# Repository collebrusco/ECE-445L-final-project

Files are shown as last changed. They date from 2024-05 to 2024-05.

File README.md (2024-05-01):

# ECE445L Final Lab
Final project for Spring '24 ECE 445L (1st place winner!)    
Frank Collebrusco, Rocco Perciavalle, Connor Leu, Sajid Bhuiyan      

Remote-controlled drag racing! Players use two controllers to drive the dragsters. The controllers have a throttle and a gear shifter, and the players must time their gear shifts for the optimal power output. The controller software simulates engine operation and the resulting power output. Players are penalized for red-lining, shifting too early or too late. The better driver wins!   

team photo

dragsters   

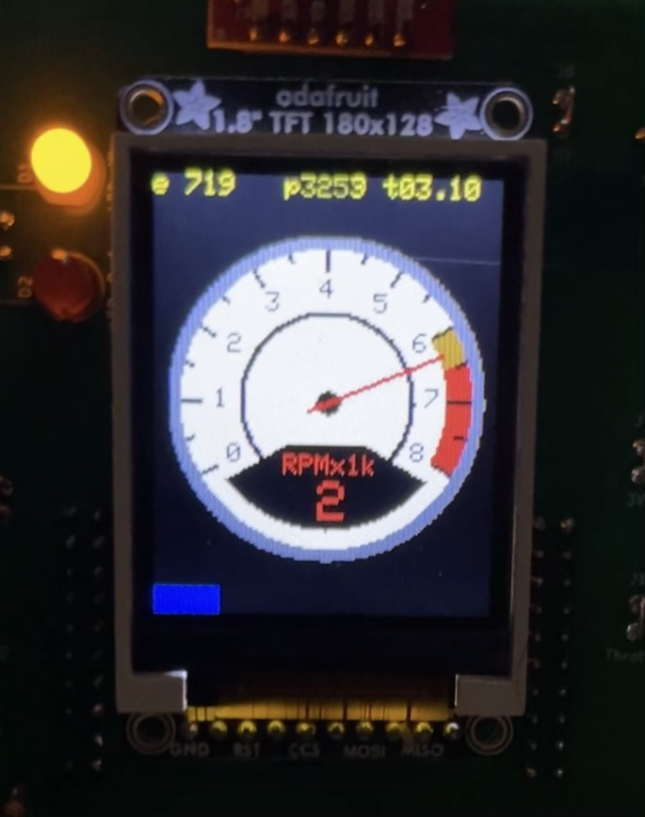
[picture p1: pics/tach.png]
tach


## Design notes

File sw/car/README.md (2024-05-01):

# README

This is the template project folder for your lab. Feel free to modify the files
in here, as long as they remain in this folder. This is where TAs will look for
when running your project and/or inspecting your code for software quality.

## Creating a New Project (Keil)

1. Open up Keil.
2. Click on the 'Project' tab on the top toolbar.
3. Click on New uVision Project.
4. Create a new .uvproj file of the desired name (typically Lab1, Lab5, etc) in the SW folder.
5. Search for the 'TM4C123GH6PM' device in the 'Select Device for Target 'Target 1' window.
6. Press OK and then press OK again in the 'Manage Run-Time Environment' window. 

## Managing Project Files

1. Right click on the 'Target 1' item in the Project sidebar window.
2. Click on 'Manage Project Items' in the submenu.
3. In the 'Files' column, click on the 'Add Files' button.
4. Add the implementation files (.C and .s files) required for the project
   dependencies into the project. This includes your main file. In particular,
   make sure you include the startup.s file, since this includes things like
   interrupt definitions.

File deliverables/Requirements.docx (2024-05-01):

## Project Requirements Document:

1) Overview
  a) Objectives: Why are we doing this project? What is the purpose?

The goal of this project is to combine what we’ve learned through the labs in this class as well as prior 319K knowledge into a coherent embedded system. The project provides a more open-ended scenario than the other labs which allows us to build a more creative system and see the creativity of other groups.

  b) Interactions with Existing Systems: Include this if you are connecting to another board

Aside from using multiple TM4Cs, we will be interfacing via UART with ESP8266 microcontrollers for wireless communication. The goal is to minimize complexity of the networking protocol and have two ESP microcontrollers communicating with each other directly.

  c) Terminology: Define domain specific terms used in the document.

None.

2) Functional Description
  a) Functionality: What will the system do precisely?

The system is a slot-car racing game. The game is two players, each with a car on a racetrack. Skill from the game is derived from controlling your speed around turns (you need to avoid flying off the track!) and timing your “shifting” to maximize your speed. The system will have two controllers that wirelessly communicate with their car, and a central TM4C for timing and/or counting laps, declaring the winner, and potentially additional stretch-goals.

  b) Performance: Define the measures and describe how they will be determined.

Performance of this system will be measured through controller latency, timing latency, and speed and maneuverability of the cars. Controller latency could be measured via synchronous clocks on each system, and seeing the time elapsed between an input and seeing movement on the car, or through a slow-motion video. Speed an maneuverability of the cars can be measured by simply observing them move around the track.

  c) Usability: Describe the interfaces. Be quantitative if possible

The main interfaces for the users in the system are the controllers. There will be two sets of controls, one for each car. The controller will not be battery operated. Instead, it will be wired to the track. The controllers will then communicate wirelessly to the cars. As a stretch goal, we intend to have speedometers and other metrics on LCDs as part of the controller.

3) Deliverables
  a) Roles and Responsibilities: Who will do what? What is the purpose?

Conner Leu will be largely responsible for designing the PCBs, and sourcing components. Frank Collebrusco and Sajid Bhuiyan will work heavily on the software managing wireless, timing, and potentially graphical systems. Rocco Perciavalle will work on 3D CAD models for the car chassis. All members will provide support across all aspects of the project, including building the track, cars, controllers, and software.

  b) Reports: Simply state the reports for Labs 7 and 11 will be written

Reports for Labs 7 and 11 will be written.

  c) Outcomes: What are the deliverables? How do we know when it is done?

The project is done once we have two functional cars and controllers that communicate wirelessly, along with a central controller to manage laps and timing. Any additional features are stretch goals.

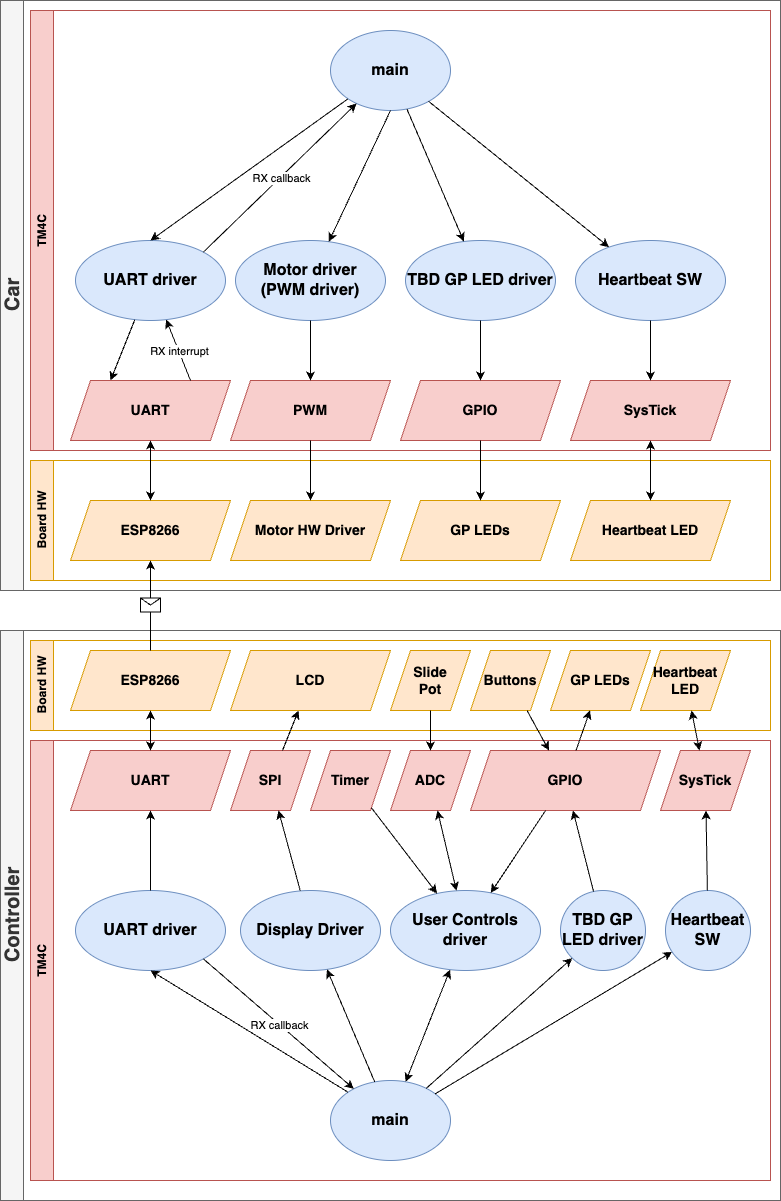
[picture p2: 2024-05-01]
deliverables/SystemDiagram.png

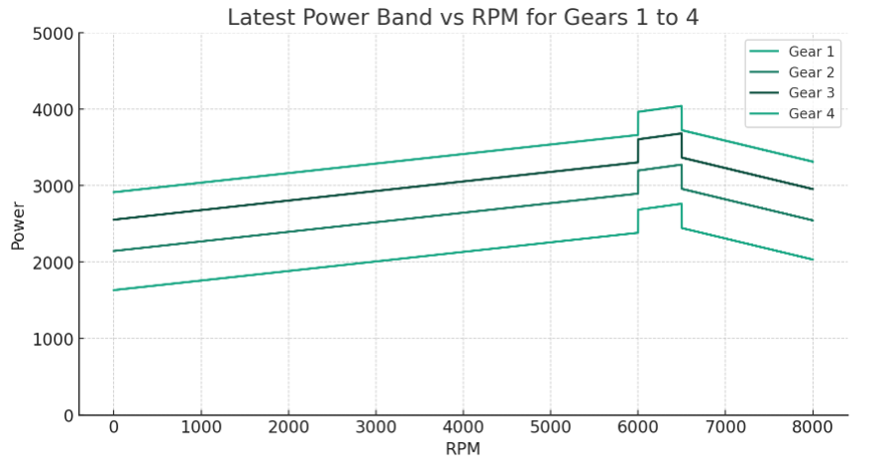
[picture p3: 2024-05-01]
sw/PWM_12bit_by_rpm_gear.PNG

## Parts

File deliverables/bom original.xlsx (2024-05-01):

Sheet: Parts
Bill of Materials |  |  | 2022-03-10 | "not free" means you have to buy it |  | "free sample" means you have to order it
EE445L Spring 2022 |  |  | EE445L pays for the PCB | "Cabinet means in one of the six black cabinets in professsor's office (bring a print out of your SCH")
 |  |  |  | "Professor" means ask your professor quantity and style will vary (bring a print out of your SCH circuit)
Qty Note | REF DES Note (http://projects.ece.utexas.edu/valvano/wiki/doku.php?id=pcbartist:schematics) |  |  | "Box means in box in your professor's office (bring a print out of your SCH circuit)
Quantity | REF DES | Type | Description | Manufacturer | Mfg. P/N | Distributor | P/N | Unit cost | Cost |  | Where to get it? | Inventory
0 |  | ASM | 8-ohm speaker |  |  | AllElectronics | SK-840 | $0.60 | $0.00 | Speaker | professor | https://www.allelectronics.com/item/sk-840/speaker-8-ohm-40mm/1.html
0 |  | ASM | 9V battery snap, T-type |  |  | AllElectronics | BST-61 | $0.50 | $0.00 | Jumper2 | Box
0 |  | ASM | Black case, 5.5" x 2.6" x 1.1" | Hammond | 1593YALBK | Mouser | 546-1593YALBK | $8.50 | $0.00 |  |  | http://www.hammondmfg.com/pdf/1593Y.pdf
0 |  | ASM | Black Case 5.620" x 3.250" X 1.500" | Serpac | 151 | Digikey | SR151B-ND | $10.88 | $0.00 |  | professor
0 |  | ASM | Black case, 7.5" by 4.3" by 2.2" | Hammond | 1591ESBK | Mouser | 546-1591ES-BK | $8.71 | $0.00 |  | Box | http://www.hammondmfg.com/pdf/1591E.pdf
0 |  | ASM | Electret microphone | Panasonic |  | AllElectronics | MIKE-79 | $0.50 | $0.00 | electret | Cabinet
0 |  | CAP | Ceramic, X7R, 20%, 1 uF |  |  | Jameco | 81509 | $0.35 | $0.00 | Ceramic0.2 | Cabinet
0 |  | CAP | Ceramic, Z5U, -20/+80%, 0.47 uF | Kemet | C320C474M5U5TA | Digikey | 399-4309-ND | $0.40 | $0.00 | Ceramic | Cabinet
0 |  | CAP | Ceramic, Z5U, -20/+80%, 0.1 uF |  |  | Digikey | 399-4151-ND | $0.04 | $0.00 | Ceramic | Cabinet
0 |  | CAP | Ceramic, Z5U, -20/+80%, 0.033 uF |  |  | Digikey | 399-4298-ND | $0.40 | $0.00 | Ceramic | Cabinet
0 |  | CAP | Ceramic, Z5U, -20/+80%, 0.027uF |  |  |  |  | $0.40 | $0.00 | Ceramic | Cabinet
0 |  | CAP | Ceramic, Z5U, -20/+80%, 0.01 uF |  |  | Digikey | 399-4148-ND | $0.40 | $0.00 | Ceramic | Cabinet
0 |  | CAP | Ceramic, Z5U, -20/+80%, 4.7 nF |  |  | Digikey | 399-4188-ND | $0.40 | $0.00 | Ceramic | Cabinet
0 |  | CAP | Ceramic, Z5U, -20/+80%, 2.2 nF |  |  |  |  | $0.40 | $0.00 | Ceramic | Cabinet
0 |  | CAP | Ceramic, Z5U, -20/+80%, 1 nF |  |  |  |  | $0.40 | $0.00 | Ceramic | Cabinet
0 |  | CAP | Ceramic Z5U, -20/+80%, 470 pF |  |  |  |  | $0.03 | $0.00 | Ceramic | Cabinet
0 |  | CAP | Ceramic Z5U, -20/+80%, 330 pF |  |  |  |  | $0.03 | $0.00 | Ceramic | Cabinet
0 |  | CAP | Ceramic Z5U, -20/+80%, 220 pF |  |  |  |  | $0.03 | $0.00 | Ceramic | Cabinet
0 |  | CAP | Ceramic Z5U, -20/+80%, 100 pF |  |  |  |  | $0.03 | $0.00 | Ceramic | Cabinet
0 |  | CAP | Ceramic Z5U, -20/+80%, 22 pF |  |  |  |  | $0.03 | $0.00 | Ceramic | Cabinet
0 |  | CAP | Ceramic C0G, 10%, 10 pF | Murata 50V 5% | RDE5C1H100J0P1H03B | Digikey | 490-8629-ND | $0.31 | $0.00 | Ceramic | Cabinet | not required, we expect most students will create a system with the LaunchPad
0 |  | CAP-Tant | Tantalum, 16V, 20% 2.2 uF | AVX Corporation | TAP225M016CCS | Digikey | 478-8819-ND | $0.29 | $0.00 | tantalum | Cabinet
0 |  | CAP-Tant | Tantalum, 16V, 10% 4.7 uF |  |  | Digikey | 478-1904-ND | $0.22 | $0.00 | tantalum | Cabinet
0 |  | CAP-Tant | Tantalum, 20V, 10%, 1 uF |  |  | Digikey | 478-1833-ND | $0.32 | $0.00 | tantalum | Cabinet
0 |  | CAP-Tant | Tantalum, 20V 10%, 10uF |  |  | Digikey | 478-1840-ND | $0.56 | $0.00 | tantalum | Cabinet
0 |  | CAP-Tant | Tantalum, 35V, 10%, 0.47 uF |  |  | Jameco | 33531 | $0.19 | $0.00 | tantalum | Cabinet
0 |  | CAP-Elec | Electrolytic, 16V, 100 uF, cap 20%, ESR=20mV |  |  | Mouser | 661-APSF160E101MF05S | $0.38 | $0.00 | tantalum | Cabinet
0 |  | CON | 2 to 40 pin 0.1 in header (price per pin) |  |  | AllElectronics | SHS-40 | $0.02 | $0.00 | Jumper2 | Cabinet | https://www.allelectronics.com/item/shs-40/1-x-40-header-0.1-spacing/1.html
0 |  | CON | 2-pin shrouded header (mates with SBC-2) |  |  | AllElectronics | SBH-2 | $0.10 | $0.00 | Jumper2 | Cabinet | https://www.allelectronics.com/item/sbh-2/header-for-small-battery-conn-2.5mm-spacing/1.html
0 |  | CON | 2-pin battery cable (mates with SBH-2) |  |  | AllElectronics | SBC-2 | $0.27 | $0.00 | goes with SBH-2 | Cabinet | https://www.allelectronics.com/item/sbc-2/small-battery-connector-2.5mm-spacing/1.html
0 |  | CON | 2-pin shorting jumper, attaches to 0.1" male-male header | Harwin | M7581-05 | Mouser | 855-M7581-05 | $0.11 | $0.00 | goes with Jumper2 | Cabinet
0 |  | CON | Test point, black | Keystone Electronics | 5001 | Digikey | 36-5001K-ND | $0.23 | $0.00 | testpoint | Cabinet
0 |  | CON | Test point, orange | Keystone Electronics | 5003 | Digikey | 36-5003K-ND | $0.23 | $0.00 | testpoint | Cabinet
0 |  | CON | Test point, yellow | Keystone Electronics | 5004 | Digikey | 36-5004K-ND | $0.23 | $0.00 | testpoint | Cabinet
0 |  | CON | Test point, white | Keystone Electronics | 5002 | Digikey | 36-5002K-ND | $0.23 | $0.00 | testpoint | Cabinet
0 |  | CON | Test point, blue | Keystone Electronics | 5117 | Digikey | 36-5117-ND | $0.23 | $0.00 | testpoint | Cabinet
0 |  | CON | Test point, green | Keystone Electronics | 5116 | Digikey | 36-5116-ND | $0.23 | $0.00 | testpoint | Cabinet
0 |  | CON | Test point, red | Keystone Electronics | 5000 | Digikey | 36-5000K-ND | $0.23 | $0.00 | testpoint | Cabinet
0 |  | CON | 10-pin female connector | SamTec | BCS-110-L-S-TE | Digikey | SAM1011-10-ND | $1.98 | $0.00 |  | Cabinet
0 |  | CON | Socket for micro SD card | Molex | 473340001 | Digikey | WM3288CT-ND | $4.02 | $0.00 | MicroSD Slot | Cabinet | do not use, rather included on ST7735
0 |  | CON | USB Mini-B socket, board mount, surface mount | Molex | 56579-0576 | Mouser | 538-56579-0576 | $2.46 | $0.00 | USB_Mini-B | Cabinet
0 |  | CON | Micro USB Type B, surface mount | Hirose Connector | ZX62D-B-5PA8(30) | Mouser | 798-ZX62D-B-5PA830 | $0.47 | $0.00 | USB_Micro-B | Cabinet
0 |  | CON | USB Mini-B socket, board mount, through hole | Molex | 54819-0519 | Digikey | WM17115-ND | $0.65 | $0.00 | USB_Mini-B | Cabinet
0 |  | CON | BoosterPack connector | FCI | 67996-220HLF | Mouser | 609-3243-ND | $0.26 | $0.00 | BoosterPack | Cabinet
0 |  | CON | Logic Analyzer connector | FCI | 68021-208HLF | Digikey | 609-3344-ND | $0.27 | $0.00 | LogicAnalyzer | Cabinet
0 |  | CON | JTAG 1 by 5 male header |  |  |  |  | $0.29 | $0.00 | JTAG | Cabinet
0 |  | CON | 10 pin 2mm socket for Xbee (need two) | SamTec | SQT-110-01-F-S | Digikey | SAM9989-ND | $2.70 | $0.00 | XbeeModule | Cabinet
0 |  | CPU | TM4C123GH6PM 64-pin LQFP | TI | TM4C123GH6PMI | Mouser | 595-TM4C123GH6PMI | $11.55 | $0.00 | TM4C123GH6PM |  | not required, we expect most students will create a system with the LaunchPad
0 |  | CRYS | NX5032GA-16.000000 | NDK | NX5032GA-16.000000 | Digikey | 644-1037-1-ND | $0.51 | $0.00 | XTAL/NX5032 | Cabinet | not required, we expect most students will create a system with the LaunchPad
0 |  | DIODE | 1N914 diode | Fairchild | 1N914 | Digikey | 1N914B-ND | $0.05 | $0.00 | 1N914 | Cabinet
0 |  | IC | LM2937 3.3 V regulator TO220, 500mA | TI | LM2937ET-3.3/NOPB | Digikey | LM2937ET-3.3-ND | $1.17 | $0.00 | LM2937-3.3 | Cabinet
0 |  | IC | LP2950 3.3V regulator, 100 mA TO-92 | TI | LP2950-33LPRE3 | Digikey | 296-31455-1-ND | $0.19 | $0.00 | LP2950-CZ-3.3 | Cabinet
0 |  | IC | 78M05 500mA 5V TO-220 regulator | National | LM78M05 | Jameco | 192233 | $0.19 | $0.00 | LM7805CT | Cabinet
0 |  | IC | OPA4350 quad op amp | TI | OPA4350UA | Mouser | 595-OPA4350UA | $12.15 | $0.00 | OPA4350 | not free
0 |  | IC | TLV5616 12-bit DAC | TI | TLV5616CP | Mouser | 595-TLV5616CP | $10.09 | $0.00 | TLV5616 | not free
0 |  | IC | TLV5618 dual 12-bit DAC | TI | TLV5618 | Mouser | TLV5618ACP | $14.18 | $0.00 | TLV5618 | not free
0 |  | IC | INA122P instrumentation amp | TI | INA122P | Mouser | 595-INA122P | $9.09 | $0.00 | INA122 | Cabinet or free sample
0 |  | IC | OPA2350 dual op amp | TI | OPA2350PA | obsolete |  |  | $0.00 | OPA2350 | Cabinet or free sample |  |  | 1 KD
0 |  | IC | TLC2274 quad op amp | TI | TLC2274ACN | Mouser | 595-TLC2274ACN | $3.06 | $0.00 | TLC2274 | not free |  |  | 2 HD
0 |  | IC | TPA731 audio amp (pin 1 low) 700mW | TI | TPA731D | Mouser | 595-TPA731D | $2.90 | $0.00 | TPA731 | not free |  |  | 3 AD
0 |  | IC | TPA751 audio amp (pin 1 high) 700mW | TI | TPA751D | Mouser | 595-TPA751D | $2.31 | $0.00 | TPA731 | not free |  |  | 4 JD
0 |  | IC | LM4041CILPR shunt diode reference | TI | LM4041CILPR | Mouser | 595-LM4041CILPR | $1.21 | $0.00 | LM4041 | Cabinet or free sample |  |  | 5 CD
0 |  | IC | L293 Motor H bridge | TI | L293NE | Digikey | 296-9519-5-ND | $3.50 | $0.00 | L293 | Cabinet |  |  | 7 MD
0 |  | IC | 74HC595 |  |  | Jameco | 46105 | $0.40 | $0.00 |  | Cabinet |  |  | 8 ED
0 |  | IC | 74HC165 |  |  | Jameco | 45495 | $0.30 | $0.00 |  | Cabinet |  |  | 9 FD
0 |  | IC | 74HCT125N | TI | SN74HCT125N | Mouser | 595-SN74HCT125N | $0.53 | $0.00 |  | Cabinet
0 |  | IC | RS232 driver | STMicroelectronics | ST232CN | Jameco | 2001171 | $0.58 | $0.00 | ST232 | Cabinet |  |  | 0 ND
0 |  | JACK | DC Power MALE 2.1mm |  |  | Jameco | 101179 | $0.55 | $0.00 | PowerJack | Cabinet |  |  | * LD
0 |  | JACK | Stereo Jack, or audio jack |  |  | AllElectronics | MJW-12 | $0.09 | $0.00 | HeadphoneJack | Cabinet |  | 87YY3212A
0 |  | KEY | 3 by 4 common bus (D), keypad | Grayhill | 87YY3212A-506 |  |  | $2.99 | $0.00 | 87YY3212A | Box | http://docs.bgmicro.com/pdf/swt1109.pdf
0 |  | LCD | 18-bit color 128*160 1.8" TFT LCD display | Sitronix | ST7735R | Adafruit | 358 | $19.96 | $0.00 | ST7735 | not free
0 |  | LED | Green 2mA 5mm diffused | Avago Technologies | HLMP-4740 | Digikey | 516-1327-ND | $0.29 | $0.00 | LEDT1.75 | Cabinet
0 |  | LED | Red 1.6V 1mA 5mm diffused | Avago Technologies | HLMP-D150 | Digikey | 516-1323-ND | $0.29 | $0.00 | LEDT1.75 | Cabinet
0 |  | LED | Yellow 2mA 5mm diffused | Avago Technologies | HLMP-4719 | Digikey | 516-1326-ND | $0.29 | $0.00 | LEDT1.75 | Cabinet
0 |  | LED | Orange 10mA 5mm diffused | Avago Technologies | HLMP-D401 | Digikey | 516-1330-ND | $0.29 | $0.00 | LEDT1.75 | Cabinet
0 |  | LED | Blue 10mA 5mm diffused |  |  |  |  | $0.99 | $0.00 | LEDT1.75 | Cabinet | warning, the blue LEDs are very bright
0 |  | PCB | PCB plus shipping | JLCPCB |  | JLCPCB |  | $13.00 | $0.00
0 |  | POT | 20K LINEAR SLIDE POT | Bourns | PTA2043-2015CPB103 | Mouser | 652-PTA20432015CPB10 | $1.28 | $0.00 |  | Cabinet
0 |  | POT | 10 K one-turn potentiometer |  |  |  |  | $0.15 | $0.00 | SquarePot | Professor
0 |  | POT | 20 K one-turn potentiometer |  |  |  |  | $0.15 | $0.00 | SquarePot | Professor
0 |  | RES | Carbon 1/6W, 5%, 100 | Yageo | CFR-12JB-100R | Digikey | 100EBK-ND | $0.02 | $0.00 | 0.125Wresistor | Cabinet
0 |  | RES | Carbon 1/6W, 5%, 220 | Yageo | CFR-12JB-220R | Digikey | 220EBK-ND | $0.02 | $0.00 | 0.125Wresistor | Cabinet
0 |  | RES | Carbon 1/6W, 5%, 270 | Yageo | CFR-12JB-270R | Digikey | 270EBK-ND | $0.02 | $0.00 | 0.125Wresistor | Cabinet
0 |  | RES | Carbon 1/6W, 5%, 330 | Yageo | CFR-12JB-330R | Digikey | 330EBK-ND | $0.02 | $0.00 | 0.125Wresistor | Cabinet
0 |  | RES | Carbon 1/6W, 5%, 470 | Yageo | CFR-12JB-470R | Digikey | 470EBK-ND | $0.02 | $0.00 | 0.125Wresistor | Cabinet
0 |  | RES | Carbon 1/6W, 5%, 510 | Yageo | CFR-12JB-510R | Digikey | 510EBK-ND | $0.02 | $0.00 | 0.125Wresistor | Cabinet
0 |  | RES | Carbon 1/6W, 5%, 680 | Yageo | CFR-12JB-680R | Digikey | 680EBK-ND | $0.02 | $0.00 | 0.125Wresistor | Cabinet
0 |  | RES | Carbon 1/6W, 5%, 820 | Yageo | CFR-12JB-820R | Digikey | 820EBK-ND | $0.02 | $0.00 | 0.125Wresistor | Cabinet
0 |  | RES | Carbon 1/6W, 5%, 1K | Yageo | CFR-12JB-1K0 | Digikey | 1.0KEBK-ND | $0.02 | $0.00 | 0.125Wresistor | Cabinet
0 |  | RES | Carbon 1/6W, 5%, 1.2K | Yageo | CFR-12JB-1K2 | Digikey | 1.2KEBK-ND | $0.02 | $0.00 | 0.125Wresistor | Cabinet
0 |  | RES | Carbon 1/6W, 5%, 1.5K | Yageo | CFR-12JB-1K5 | Digikey | 1.5KEBK-ND | $0.02 | $0.00 | 0.125Wresistor | Cabinet
0 |  | RES | Carbon 1/6W, 5%, 1.8K | Yageo | CFR-12JB-1K8 | Digikey | 1.8KEBK-ND | $0.02 | $0.00 | 0.125Wresistor | Cabinet
0 |  | RES | Carbon 1/6W, 5%, 2.0K | Yageo | CFR-12JB-2K0 | Digikey | 2.0KEBK-ND | $0.02 | $0.00 | 0.125Wresistor | Cabinet
0 |  | RES | Carbon 1/6W, 5%, 2.2K | Yageo | CFR-12JB-2K2 | Digikey | 2.2KEBK-ND | $0.02 | $0.00 | 0.125Wresistor | Cabinet
0 |  | RES | Carbon 1/6W, 5%, 2.7K | Yageo | CFR-12JB-2K7 | Digikey | 2.7KEBK-ND | $0.02 | $0.00 | 0.125Wresistor | Cabinet
0 |  | RES | Carbon 1/6W, 5%, 3.3K | Yageo | CFR-12JB-3K3 | Digikey | 3.3KEBK-ND | $0.02 | $0.00 | 0.125Wresistor | Cabinet
0 |  | RES | Carbon 1/6W, 5%, 3.9K | Yageo | CFR-12JB-3K9 | Digikey | 3.9KEBK-ND | $0.02 | $0.00 | 0.125Wresistor | Cabinet
0 |  | RES | Carbon 1/6W, 5%, 4.7K | Yageo | CFR-12JB-4K7 | Digikey | 4.7KEBK-ND | $0.02 | $0.00 | 0.125Wresistor | Cabinet
0 |  | RES | Carbon 1/6W, 5%, 5.1K | Yageo | CFR-12JB-5K1 | Digikey | 5.1KEBK-ND | $0.02 | $0.00 | 0.125Wresistor | Cabinet
0 |  | RES | Carbon 1/6W, 5%, 5.6K | Yageo | CFR-12JB-5K6 | Digikey | 5.6KEBK-ND | $0.02 | $0.00 | 0.125Wresistor | Cabinet
0 |  | RES | Carbon 1/6W, 5%, 6.8K | Yageo | CFR-12JB-6K8 | Digikey | 6.8KEBK-ND | $0.02 | $0.00 | 0.125Wresistor | Cabinet
0 |  | RES | Carbon 1/6W, 5%, 8.2K | Yageo | CFR-12JB-8K2 | Digikey | 8.2KEBK-ND | $0.02 | $0.00 | 0.125Wresistor | Cabinet
0 |  | RES | Carbon 1/6W, 5%, 10K | Yageo | CFR-12JB-10K | Digikey | 10KEBK-ND | $0.02 | $0.00 | 0.125Wresistor | Cabinet
0 |  | RES | Carbon 1/6W, 5%, 12K | Yageo | CFR-12JB-12K | Digikey | 12KEBK-ND | $0.02 | $0.00 | 0.125Wresistor | Cabinet
0 |  | RES | Carbon 1/6W, 5%, 15K | Yageo | CFR-12JB-15K | Digikey | 15KEBK-ND | $0.02 | $0.00 | 0.125Wresistor | Cabinet | http://www.kemet.com/kemet/web/homepage/kechome.nsf/vapubfiles/F3101_GoldMax.pdf/$file/F3101_GoldMax.pdf
0 |  | RES | Carbon 1/6W, 5%, 18K | Yageo | CFR-12JB-18K | Digikey | 18KEBK-ND | $0.02 | $0.00 | 0.125Wresistor | Cabinet
0 |  | RES | Carbon 1/6W, 5%, 20K | Yageo | CFR-12JB-20K | Digikey | 20KEBK-ND | $0.02 | $0.00 | 0.125Wresistor | Cabinet
0 |  | RES | Carbon 1/6W, 5%, 22K | Yageo | CFR-12JB-22K | Digikey | 22KEBK-ND | $0.02 | $0.00 | 0.125Wresistor | Cabinet
0 |  | RES | Carbon 1/6W, 5%, 27K | Yageo | CFR-12JB-27K | Digikey | 27KEBK-ND | $0.02 | $0.00 | 0.125Wresistor | Cabinet
0 |  | RES | Carbon 1/6W, 5%, 36K | Yageo | CFR-12JB-36K | Digikey | 36KEBK-ND | $0.02 | $0.00 | 0.125Wresistor | Cabinet
0 |  | RES | Carbon 1/6W, 5%, 33K | Yageo | CFR-12JB-33K | Digikey | 33KEBK-ND | $0.02 | $0.00 | 0.125Wresistor | Cabinet
0 |  | RES | Carbon 1/6W, 5%, 39K | Yageo | CFR-12JB-39K | Digikey | 39KEBK-ND | $0.02 | $0.00 | 0.125Wresistor | Cabinet
0 |  | RES | Carbon 1/6W, 5%, 47K | Yageo | CFR-12JB-47K | Digikey | 47KEBK-ND | $0.02 | $0.00 | 0.125Wresistor | Cabinet
0 |  | RES | Carbon 1/6W, 5%, 51K | Yageo | CFR-12JB-51K | Digikey | 51KEBK-ND | $0.02 | $0.00 | 0.125Wresistor | Cabinet
0 |  | RES | Carbon 1/6W, 5%, 56K | Yageo | CFR-12JB-56K | Digikey | 56KEBK-ND | $0.02 | $0.00 | 0.125Wresistor | Cabinet
0 |  | RES | Carbon 1/6W, 5%, 68K | Yageo | CFR-12JB-68K | Digikey | 68KEBK-ND | $0.02 | $0.00 | 0.125Wresistor | Cabinet
0 |  | RES | Carbon 1/6W, 5%, 82K | Yageo | CFR-12JB-82K | Digikey | 82KEBK-ND | $0.02 | $0.00 | 0.125Wresistor | Cabinet
0 |  | RES | Carbon 1/6W, 5%, 100K | Yageo | CFR-12JB-100K | Digikey | 100KEBK-ND | $0.02 | $0.00 | 0.125Wresistor | Cabinet
0 |  | RES | Carbon 1/6W, 5%, 120K | Yageo | CFR-12JB-120K | Digikey | 120KEBK-ND | $0.02 | $0.00 | 0.125Wresistor | Cabinet
0 |  | RES | Carbon 1/6W, 5%, 150K | Yageo | CFR-12JB-150K | Digikey | 150KEBK-ND | $0.02 | $0.00 | 0.125Wresistor | Cabinet
0 |  | RES | Carbon 1/6W, 5%, 180K | Yageo | CFR-12JB-180K | Digikey | 180KEBK-ND | $0.02 | $0.00 | 0.125Wresistor | Cabinet
0 |  | RES | Carbon 1/6W, 5%, 200K | Yageo | CFR-12JB-200K | Digikey | 200KEBK-ND | $0.02 | $0.00 | 0.125Wresistor | Cabinet
0 |  | RES | Carbon 1/6W, 5%, 220K | Yageo | CFR-12JB-220K | Digikey | 220KEBK-ND | $0.02 | $0.00 | 0.125Wresistor | Cabinet
0 |  | RES | Carbon 1/6W, 5%, 240K | Yageo | CFR-12JB-240K | Digikey | 240KEBK-ND | $0.02 | $0.00 | 0.125Wresistor | Cabinet
0 |  | RES | Carbon 1/6W, 5%, 270K | Yageo | CFR-12JB-270K | Digikey | 270KEBK-ND | $0.02 | $0.00 | 0.125Wresistor | Cabinet
0 |  | RES | Carbon 1/6W, 5%, 330K | Yageo | CFR-12JB-330K | Digikey | 330KEBK-ND | $0.02 | $0.00 | 0.125Wresistor | Cabinet
0 |  | RES | Carbon 1/6W, 5%, 390K | Yageo | CFR-12JB-390K | Digikey | 390KEBK-ND | $0.02 | $0.00 | 0.125Wresistor | Cabinet
0 |  | RES | Carbon 1/6W, 5%, 470K | Yageo | CFR-12JB-470K | Digikey | 470KEBK-ND | $0.02 | $0.00 | 0.125Wresistor | Cabinet
0 |  | RES | Carbon 1/6W, 5%, 510K | Yageo | CFR-12JB-510K | Digikey | 510KEBK-ND | $0.02 | $0.00 | 0.125Wresistor | Cabinet
0 |  | RES | Carbon 1/6W, 5%, 560K | Yageo | CFR-12JB-560K | Digikey | 560KEBK-ND | $0.02 | $0.00 | 0.125Wresistor | Cabinet
0 |  | RES | Carbon 1/6W, 5%, 680K | Yageo | CFR-12JB-680K | Digikey | 680KEBK-ND | $0.02 | $0.00 | 0.125Wresistor | Cabinet
0 |  | RES | Carbon 1/6W, 5%, 820K | Yageo | CFR-12JB-820K | Digikey | 820KEBK-ND | $0.02 | $0.00 | 0.125Wresistor | Cabinet
0 |  | RES | Carbon 1/6W, 5%, 1M | Yageo | CFR-12JB-1M0 | Digikey | 1.0MEBK-ND | $0.02 | $0.00 | 0.125Wresistor | Cabinet
0 |  | RES | Carbon 1/6W, 5%, 10M | Yageo | CFR-12JB-10M | Digikey | 10MEBK-ND | $0.02 | $0.00 | 0.125Wresistor | Cabinet
0 |  | SW | Tactile Switch, surface mount | C&K Components | KSC353JLFG | Mouser | 611-KSC353JLFG | $0.86 | $0.00 | KSC353JLFG | Cabinet
0 |  | SW | B3F tactile push button switch | Omron Electronics | B3F-1052 | Digikey | SW405-ND | $0.17 | $0.00 | B3F-1050 | Cabinet
0 |  | SW | Black Off board momentary push buttom |  |  | AllElectronics | MPB-5 | $0.35 | $0.00 | OffBoardSwitch | Professor
0 |  | SW | Red Off board momentary push buttom |  |  | AllElectronics | MPB-1 | $0.35 | $0.00 | OffBoardSwitch | Professor
0 |  | SW | On/off power switch |  |  |  |  | $0.85 | $0.00 | OffBoardPowerSwitch | Professor
0 |  | TRAN | PN2222 NPN transistor | Fairchild Semiconductor | PN2222 | Digikey | PN2222BU-ND | $0.13 | $0.00 | 2N2222 | Cabinet | be careful to get pins 1 and 3 correct, there are two versions of the chip: 2N2222 and PN2222
0 |  | TRAN | TIP120 Darlington NPN, TO220 | Fairchild | TIP120 | Digikey | TIP120-ND | $0.68 | $0.00 | TIP120 | Cabinet
0 |  | TRAN | TIP125 Darlington PNP, TO220 | Fairchild | TIP125 | Digikey | TIP125TU-ND | $0.67 | $0.00 | TIP125 | Cabinet
0 |  | TRAN | IRF540 MOSFET N-channel, TO220 |  | IRF540 | Digikey | IRF540NPBF-ND | $1.95 | $0.00 | IRF540 | Cabinet

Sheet: SurfaceMountParts
Quantity | REF DES | Type | Description | Manufacturer | Mfg. P/N | Distributor | P/N | Unit cost | Cost | PCB Artist | Where to get it?
0 |  | CAP | 0805 0.22 uF X7R ceramic |  |  |  |  | $0.14 | $0.00 | Ceramic0805 | Little box of surface mount parts
0 |  | CAP | 0805 220 pF C0G ceramic |  |  |  |  | $0.35 | $0.00 | Ceramic0805 | Little box of surface mount parts
0 |  | RES | 0805 1.1k 1% |  |  |  |  | $0.04 | $0.00 | 0.1WresistorSM805 | Little box of surface mount parts
0 |  | RES | 0805 10k 1% |  |  |  |  | $0.04 | $0.00 | 0.1WresistorSM805 | Little box of surface mount parts
0 |  | RES | 0805 20k 1% |  |  |  |  | $0.04 | $0.00 | 0.1WresistorSM805 | Little box of surface mount parts
0 |  | RES | 0805 25.5k 1% |  |  |  |  | $0.04 | $0.00 | 0.1WresistorSM805 | Little box of surface mount parts
0 |  | RES | 0805 100k 1% |  |  |  |  | $0.04 | $0.00 | 0.1WresistorSM805 | Little box of surface mount parts

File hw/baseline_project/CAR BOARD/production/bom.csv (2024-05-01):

Designator | Footprint | Quantity | Value | LCSC Part #
5VREG1 | TO-220-3_Vertical | 1 | LM7805_TO220
C1 | CP_Radial_Tantal200mil | 1 | 2.2uF
C10, C2, C7 | C_Axial_200mil | 3 | 0.1uF
C11, C18, C3, C8 | C_Axial_200mil | 4 | 0.01uF
C12, C15 | C_Axial_200mil | 2 | 10u
C13, C14 | C_Axial_200mil | 2 | 0.1u
C16 | C_Axial_L5.1mm_D3.1mm_P15.00mm_Horizontal | 1 | 100nF
C17 | CP_Axial_L10.0mm_D4.5mm_P15.00mm_Horizontal | 1 | 4.7uF
C19 | C_Axial_200mil | 1 | .1uF
C4, C5 | C_Axial_200mil | 2 | 10pF C0G
C6, C9 | C_Axial_200mil | 2 | 1uF
D1 | LED_D5.0mm | 1 | 3V3_LED
D2 | LED_D5.0mm | 1 | 5V_LED
D3 | D_DO-35_SOD27_P7.62mm_Horizontal | 1 | 1N914
D4 | LED_D5.0mm | 1 | HEARTBEAT
D5 | LED_D5.0mm | 1 | REDLED
D6 | LED_D5.0mm | 1 | ORNGLED
D7 | LED_D5.0mm | 1 | YLWLED
IC1 | QFP50P1200X1200X160-64N | 1 | TM4C123GH6PMIR
J1 | PinHeader_1x05_P2.54mm_Vertical | 1 | JTAG HEADER
J2, J3 | PinSocket_1x01_P2.54mm_Vertical | 2 | Conn_01x01
J6 | PinHeader_1x02_P2.54mm_Vertical | 1 | MotorOut
Q1 | DIP920W60P254L490H457Q4N | 1 | IRLD024PBF
R1 | R_Axial_DIN0204_L3.6mm_D1.6mm_P7.62mm_Horizontal | 1 | 1M
R10, R3, R7, R8, R9 | R_Axial_DIN0204_L3.6mm_D1.6mm_P7.62mm_Horizontal | 5 | 1.6k
R2, R5 | R_Axial_DIN0204_L3.6mm_D1.6mm_P7.62mm_Horizontal | 2 | 10k
R4 | R_Axial_DIN0204_L3.6mm_D1.6mm_P7.62mm_Horizontal | 1 | 3.3k
R6 | R_Axial_DIN0204_L3.6mm_D1.6mm_P7.62mm_Horizontal | 1 | 100k
SW1 | SW_PUSH_6mm | 1 | Reset
TP1 | Testpoint_1x02_P2.54mm | 1 | TP_BATT
TP2 | Testpoint_1x02_P2.54mm | 1 | TP_5V
TP3 | Testpoint_1x02_P2.54mm | 1 | TP_3V3
U1 | TO-220-3_Vertical | 1 | LM2937xT
U2 | ai_thinker_ESP8266_01 | 1 | ESP8266-01/ESP-01
Y1 | ABM3 | 1 | ABM3-16.000MHZ-B2-T

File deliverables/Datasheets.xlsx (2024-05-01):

Part Name | Desc | Datasheet link
IRF540 | High-amperage rated mosfet for motor PWM | https://www.vishay.com/docs/91021/irf540.pdf
1N914 | Diodes for back-EMF protection | https://www.vishay.com/docs/85622/1n914.pdf
Avago LED's | 4x of Red, Orange, Yellow LEDs | https://www.mouser.com/datasheet/2/678/AV02_1562EN_DS_HLMP_x15x_2021_08_25-1827993.pdf
LM78M05 | 5V LDO from battery for motor | https://www.ti.com/lit/ds/symlink/lm78m05-mil.pdf?ts=1710780071281
LM2937ET-3.3/NOPB | 3v3 LDO from battery for TM4C/ESP | https://www.ti.com/lit/ds/symlink/lm2937.pdf?ts=1710748418910
NX5032GA-16.000000 | 16MHz crystals for tm4c | https://www.mouser.com/datasheet/2/905/ndk_04232018_NX5032GA_LN_CD_1-1324922.pdf

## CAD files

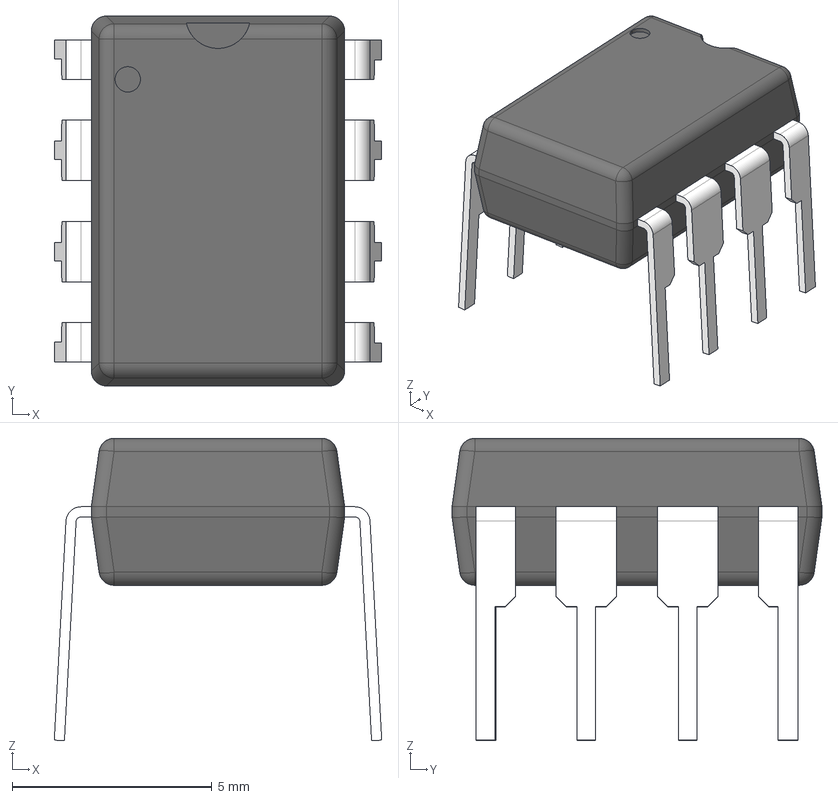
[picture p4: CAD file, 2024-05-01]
hw/baseline_project/CAR BOARD/models/ti_TLV5618AIP.stp
8.20 x 9.27 x 7.58 mm
BODY_P0008A
LEAD_P0008A x 4
LD_LHALF_P0008A x 2
LD_RHALF_P0008A x 2

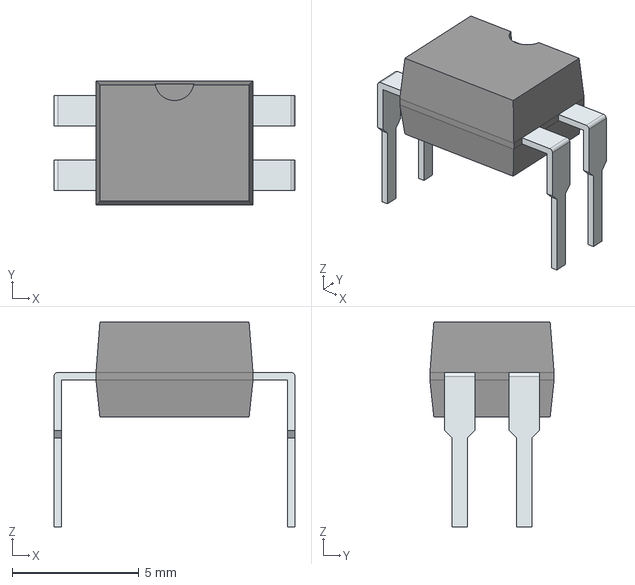
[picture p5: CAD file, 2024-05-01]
hw/baseline_project/CAR BOARD/models/vishay_IRLD024PBF.stp
9.51 x 4.90 x 8.07 mm
PinsArrayLR

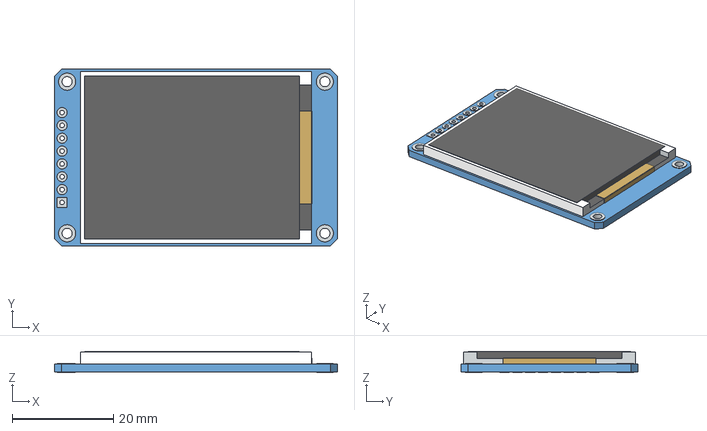
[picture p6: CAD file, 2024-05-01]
hw/baseline_project/CONTROLLER BOARD/models/adafruit_st7735r.stp
56.0 x 35.0 x 4.25 mm

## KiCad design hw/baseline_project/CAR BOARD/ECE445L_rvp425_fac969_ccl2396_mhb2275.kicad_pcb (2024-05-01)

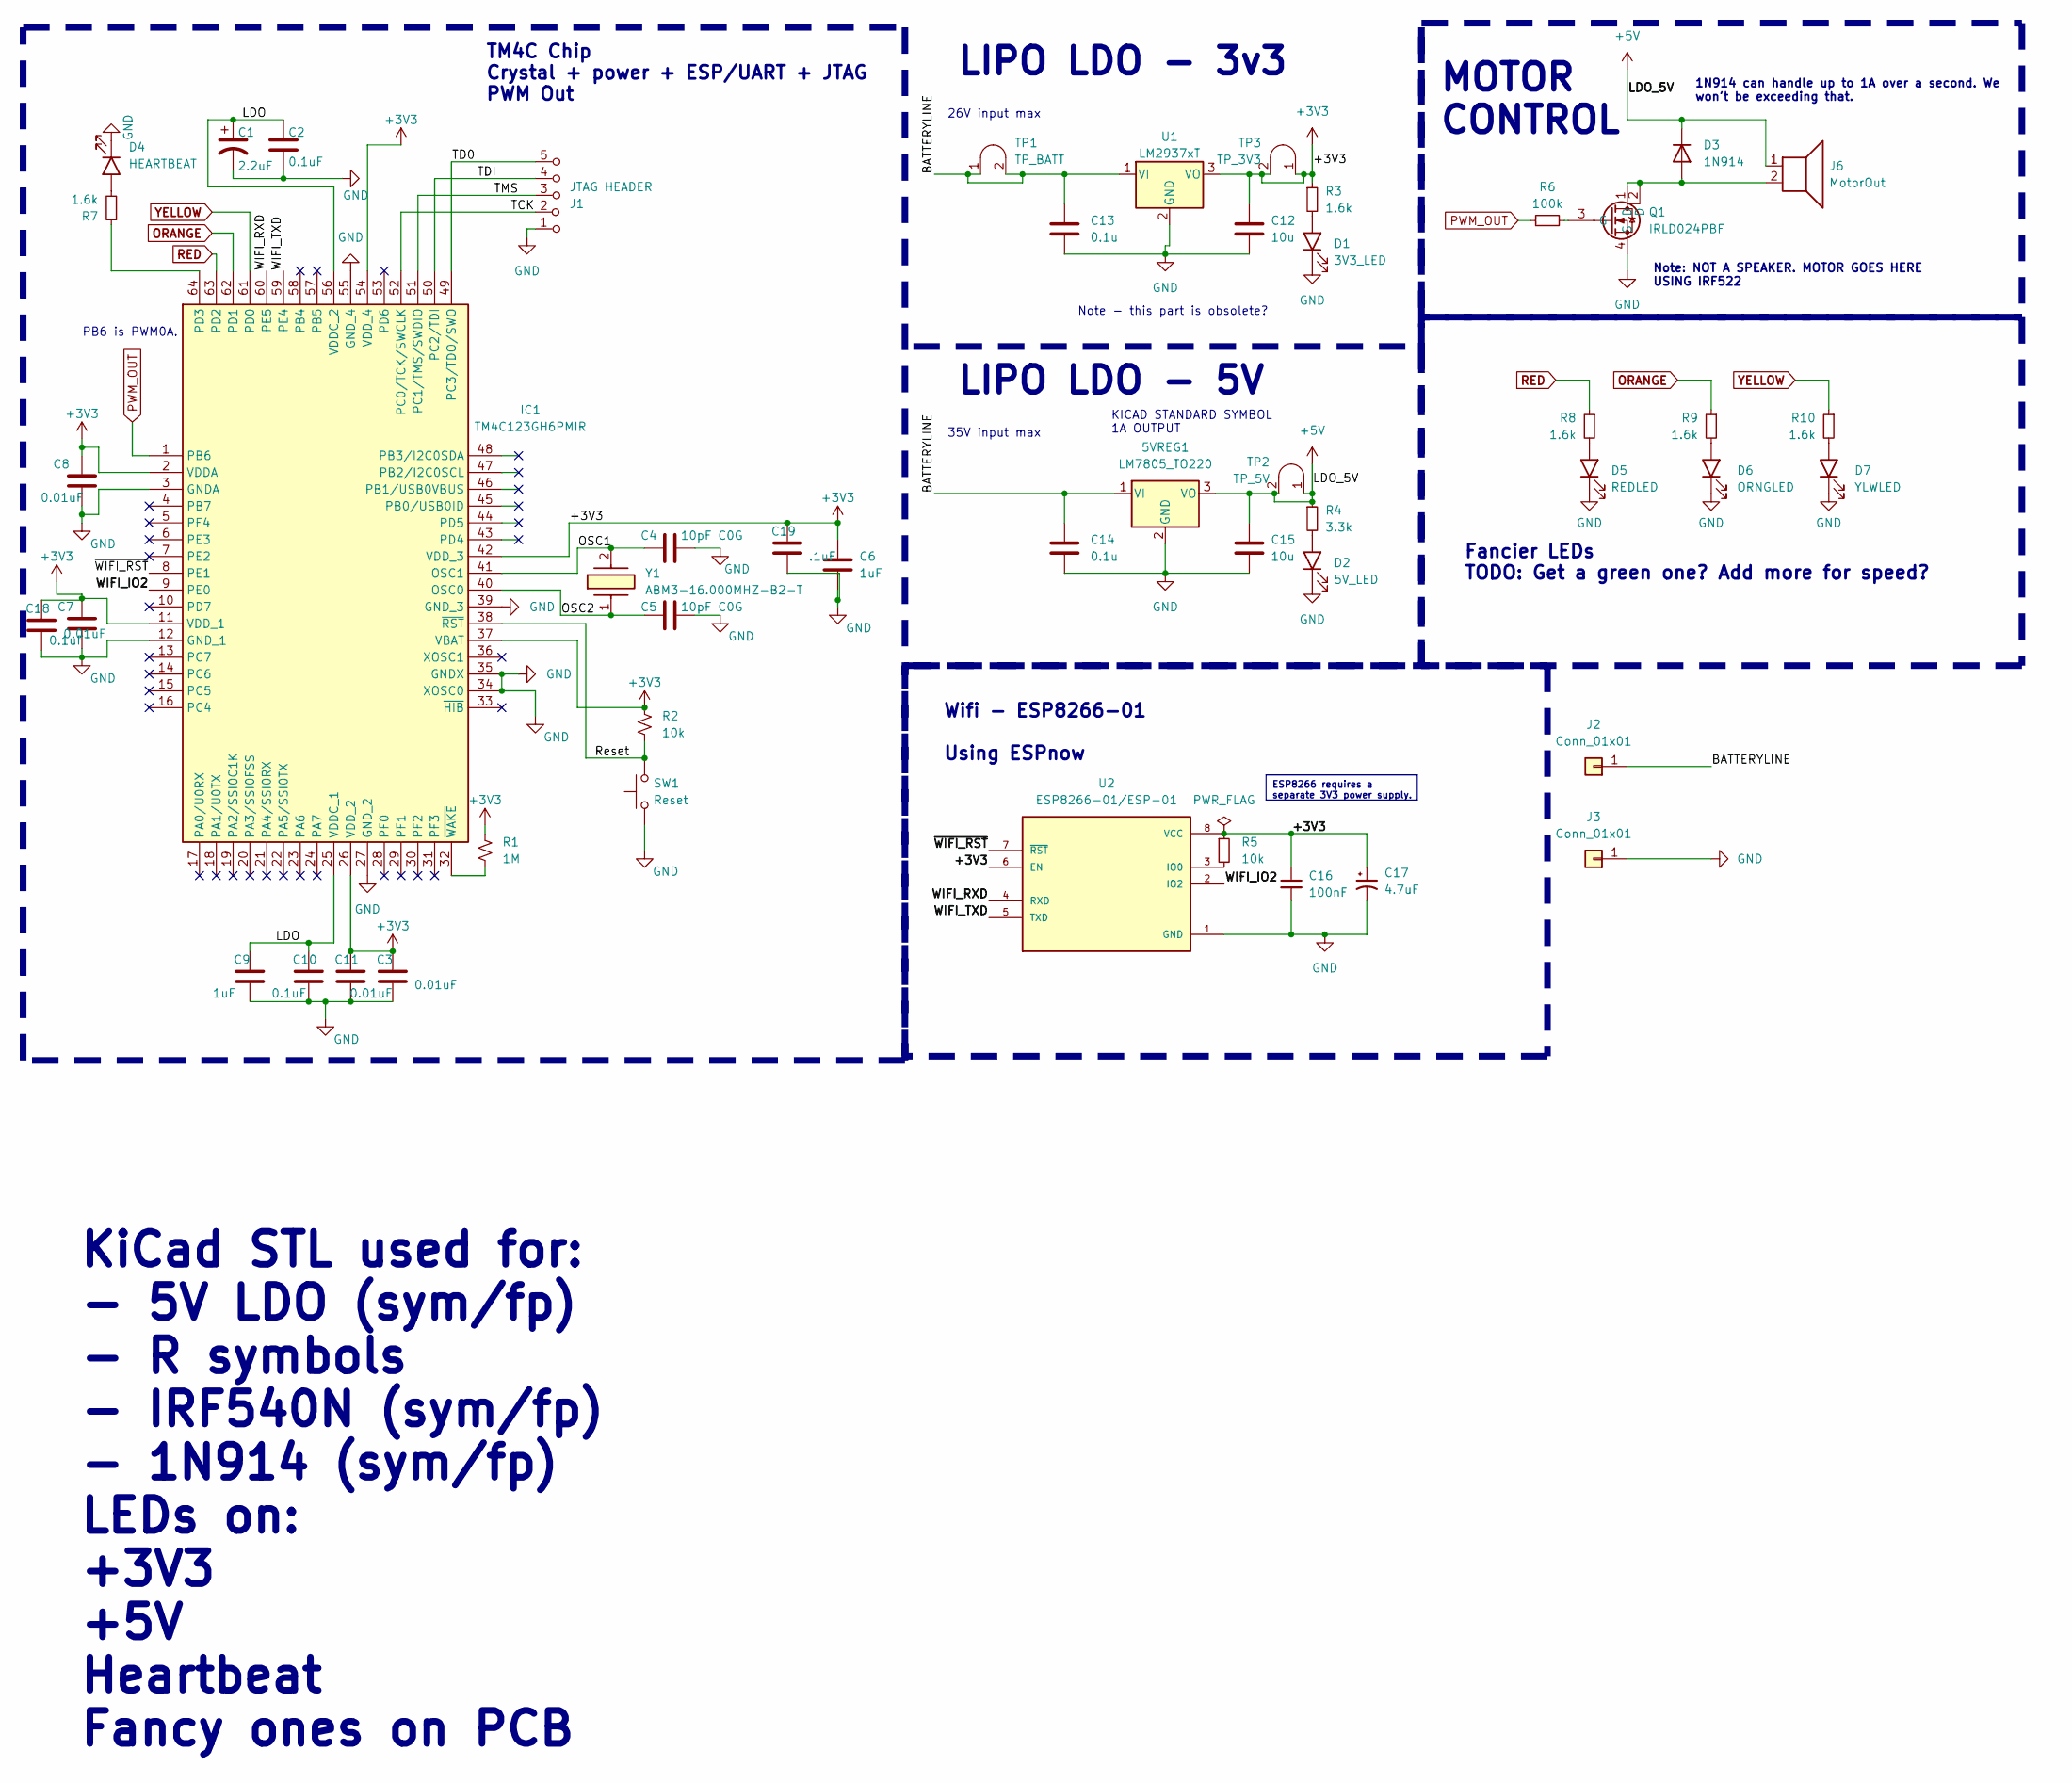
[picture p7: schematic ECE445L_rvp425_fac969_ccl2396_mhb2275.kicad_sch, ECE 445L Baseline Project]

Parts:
5VREG1: LM7805_TO220; TO-220-3_Vertical
C1: 2.2uF; CP_Radial_Tantal200mil
C2, C7, C10: 0.1uF; C_Axial_200mil
C3, C8, C11, C18: 0.01uF; C_Axial_200mil
C4, C5: 10pF C0G; C_Axial_200mil
C6, C9: 1uF; C_Axial_200mil
C12, C15: 10u; C_Axial_200mil
C13, C14: 0.1u; C_Axial_200mil
C16: 100nF; C_Axial_L5.1mm_D3.1mm_P15.00mm_Horizontal
C17: 4.7uF; CP_Axial_L10.0mm_D4.5mm_P15.00mm_Horizontal
C19: .1uF; C_Axial_200mil
D1: 3V3_LED; LED_D5.0mm
D2: 5V_LED; LED_D5.0mm
D3: 1N914; D_DO-35_SOD27_P7.62mm_Horizontal
D4: HEARTBEAT; LED_D5.0mm
D5: REDLED; LED_D5.0mm
D6: ORNGLED; LED_D5.0mm
D7: YLWLED; LED_D5.0mm
IC1: TM4C123GH6PMIR; QFP50P1200X1200X160-64N; Mouser Part Number 595-TM4C123GH6PMIR
J1: JTAG HEADER; PinHeader_1x05_P2.54mm_Vertical
J2, J3: Conn_01x01; PinSocket_1x01_P2.54mm_Vertical
J6: MotorOut; PinHeader_1x02_P2.54mm_Vertical
Q1: IRLD024PBF; DIP920W60P254L490H457Q4N; Mouser Part Number 844-IRLD024PBF
R1: 1M; R_Axial_DIN0204_L3.6mm_D1.6mm_P7.62mm_Horizontal
R2, R5: 10k; R_Axial_DIN0204_L3.6mm_D1.6mm_P7.62mm_Horizontal
R3, R7, R8, R9, R10: 1.6k; R_Axial_DIN0204_L3.6mm_D1.6mm_P7.62mm_Horizontal
R4: 3.3k; R_Axial_DIN0204_L3.6mm_D1.6mm_P7.62mm_Horizontal
R6: 100k; R_Axial_DIN0204_L3.6mm_D1.6mm_P7.62mm_Horizontal
SW1: Reset; SW_PUSH_6mm
TP1: TP_BATT; Testpoint_1x02_P2.54mm
TP2: TP_5V; Testpoint_1x02_P2.54mm
TP3: TP_3V3; Testpoint_1x02_P2.54mm
U1: LM2937xT; TO-220-3_Vertical
U2: ESP8266-01/ESP-01; ai_thinker_ESP8266_01
Y1: ABM3-16.000MHZ-B2-T; ABM3; Mouser Part Number 815-ABM3-16-B2-T

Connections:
+3V3: C3.1, C6.1, C7.1, C8.1, C11.1, C12.1, C16.1, C17.1, C18.1, C19.1, IC1.2 (VDDA), IC1.11 (VDD_1), IC1.26 (VDD_2), IC1.37 (VBAT), IC1.42 (VDD_3), IC1.54 (VDD_4), R1.1, R2.1, R3.1, R5.1, TP3.1 (A), TP3.2 (B), U1.3 (VO), U2.6 (EN), U2.8 (VCC)
+5V: 5VREG1.3 (VO), C15.1, D3.1 (K), J6.1, R4.1, TP2.1 (A), TP2.2 (B)
/BATTERYLINE: 5VREG1.1 (VI), C13.1, C14.1, J2.1, TP1.1 (A), TP1.2 (B), U1.1 (VI)
/LDO: C1.1, C2.1, C9.1, C10.1, IC1.25 (VDDC_1), IC1.56 (VDDC_2)
/OSC1: C4.1, IC1.41 (OSC1), Y1.2
/OSC2: C5.1, IC1.40 (OSC0), Y1.1
/Reset: IC1.38 (~RST), R2.2, SW1.2
/TCK: IC1.52 (PC0/TCK/SWCLK), J1.2 (B)
/TD0: IC1.49 (PC3/TDO/SWO), J1.5 (C)
/TDI: IC1.50 (PC2/TDI), J1.4 (C)
/TMS: IC1.51 (PC1/TMS/SWDIO), J1.3 (C)
/WIFI_IO2: IC1.9 (PE0), U2.2 (IO2)
/WIFI_RXD: IC1.60 (PE5), U2.4 (RXD)
/WIFI_TXD: IC1.59 (PE4), U2.5 (TXD)
/~WIFI_RST: IC1.8 (PE1), U2.7 (~RST)
GND: 5VREG1.2 (GND), C1.2, C2.2, C3.2, C4.2, C5.2, C6.2, C7.2, C8.2, C9.2, C10.2, C11.2, C12.2, C13.2, C14.2, C15.2, C16.2, C17.2, C18.2, C19.2, D1.1 (K), D2.1 (K), D4.1 (K), D5.1 (K), D6.1 (K), D7.1 (K), IC1.3 (GNDA), IC1.12 (GND_1), IC1.27 (GND_2), IC1.34 (XOSC0), IC1.35 (GNDX), IC1.39 (GND_3), IC1.55 (GND_4), J1.1 (A), J3.1, Q1.4 (S), SW1.1, U1.2 (GND), U2.1 (GND)
unnamed: D1.2 (A), R3.2
unnamed: D2.2 (A), R4.2
unnamed: D3.2 (A), J6.2, Q1.1 (D), Q1.2 (D)
unnamed: D4.2 (A), R7.2
unnamed: D5.2 (A), R8.2
unnamed: D6.2 (A), R9.2
unnamed: D7.2 (A), R10.2
unnamed: IC1.64 (PD3), R7.1
unnamed: IC1.32 (~WAKE), R1.2
unnamed: Q1.3 (G), R6.2
unnamed: R5.2, U2.3 (IO0)
ORANGE: IC1.62 (PD1), R9.1
PWM_OUT: IC1.1 (PB6), R6.1
RED: IC1.63 (PD2), R8.1
YELLOW: IC1.61 (PD0), R10.1

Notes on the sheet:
ESP8266 requires a separate 3V3 power supply.
Note - this part is obsolete?
35V input max
KICAD STANDARD SYMBOL 1A OUTPUT
TM4C Chip Crystal + power + ESP/UART + JTAG PWM Out
Fancier LEDs TODO: Get a green one? Add more for speed?
1N914 can handle up to 1A over a second. We won't be exceeding that.
LIPO LDO - 5V
KiCad STL used for: - 5V LDO (sym/fp) - R symbols - IRF540N (sym/fp) - 1N914 (sym/fp) LEDs on: +3V3 +5V Heartbeat Fancy ones on PCB
MOTOR CONTROL
Wifi - ESP8266-01 Using ESPnow
26V input max
LIPO LDO - 3v3
Note: NOT A SPEAKER. MOTOR GOES HERE USING IRF522
PB6 is PWM0A.

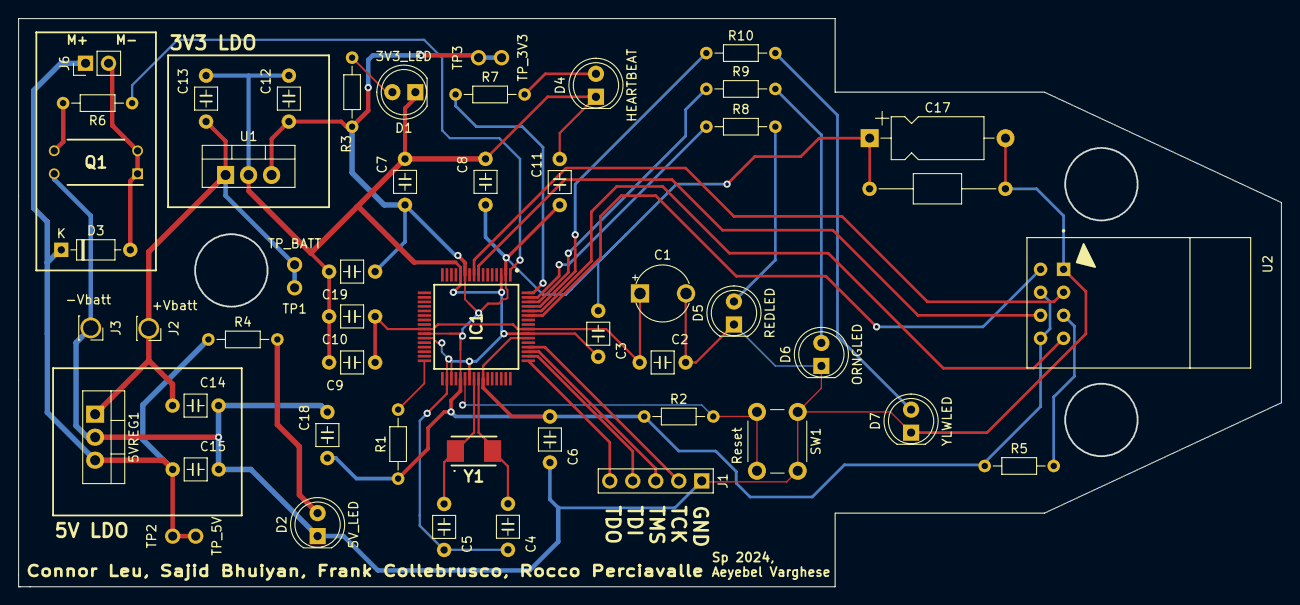
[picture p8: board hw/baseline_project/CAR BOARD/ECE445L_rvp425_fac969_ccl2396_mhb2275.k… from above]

Board: 2 copper layers, 139.4 x 62.7 mm, 50 parts (0 on the bottom side), 31 nets.

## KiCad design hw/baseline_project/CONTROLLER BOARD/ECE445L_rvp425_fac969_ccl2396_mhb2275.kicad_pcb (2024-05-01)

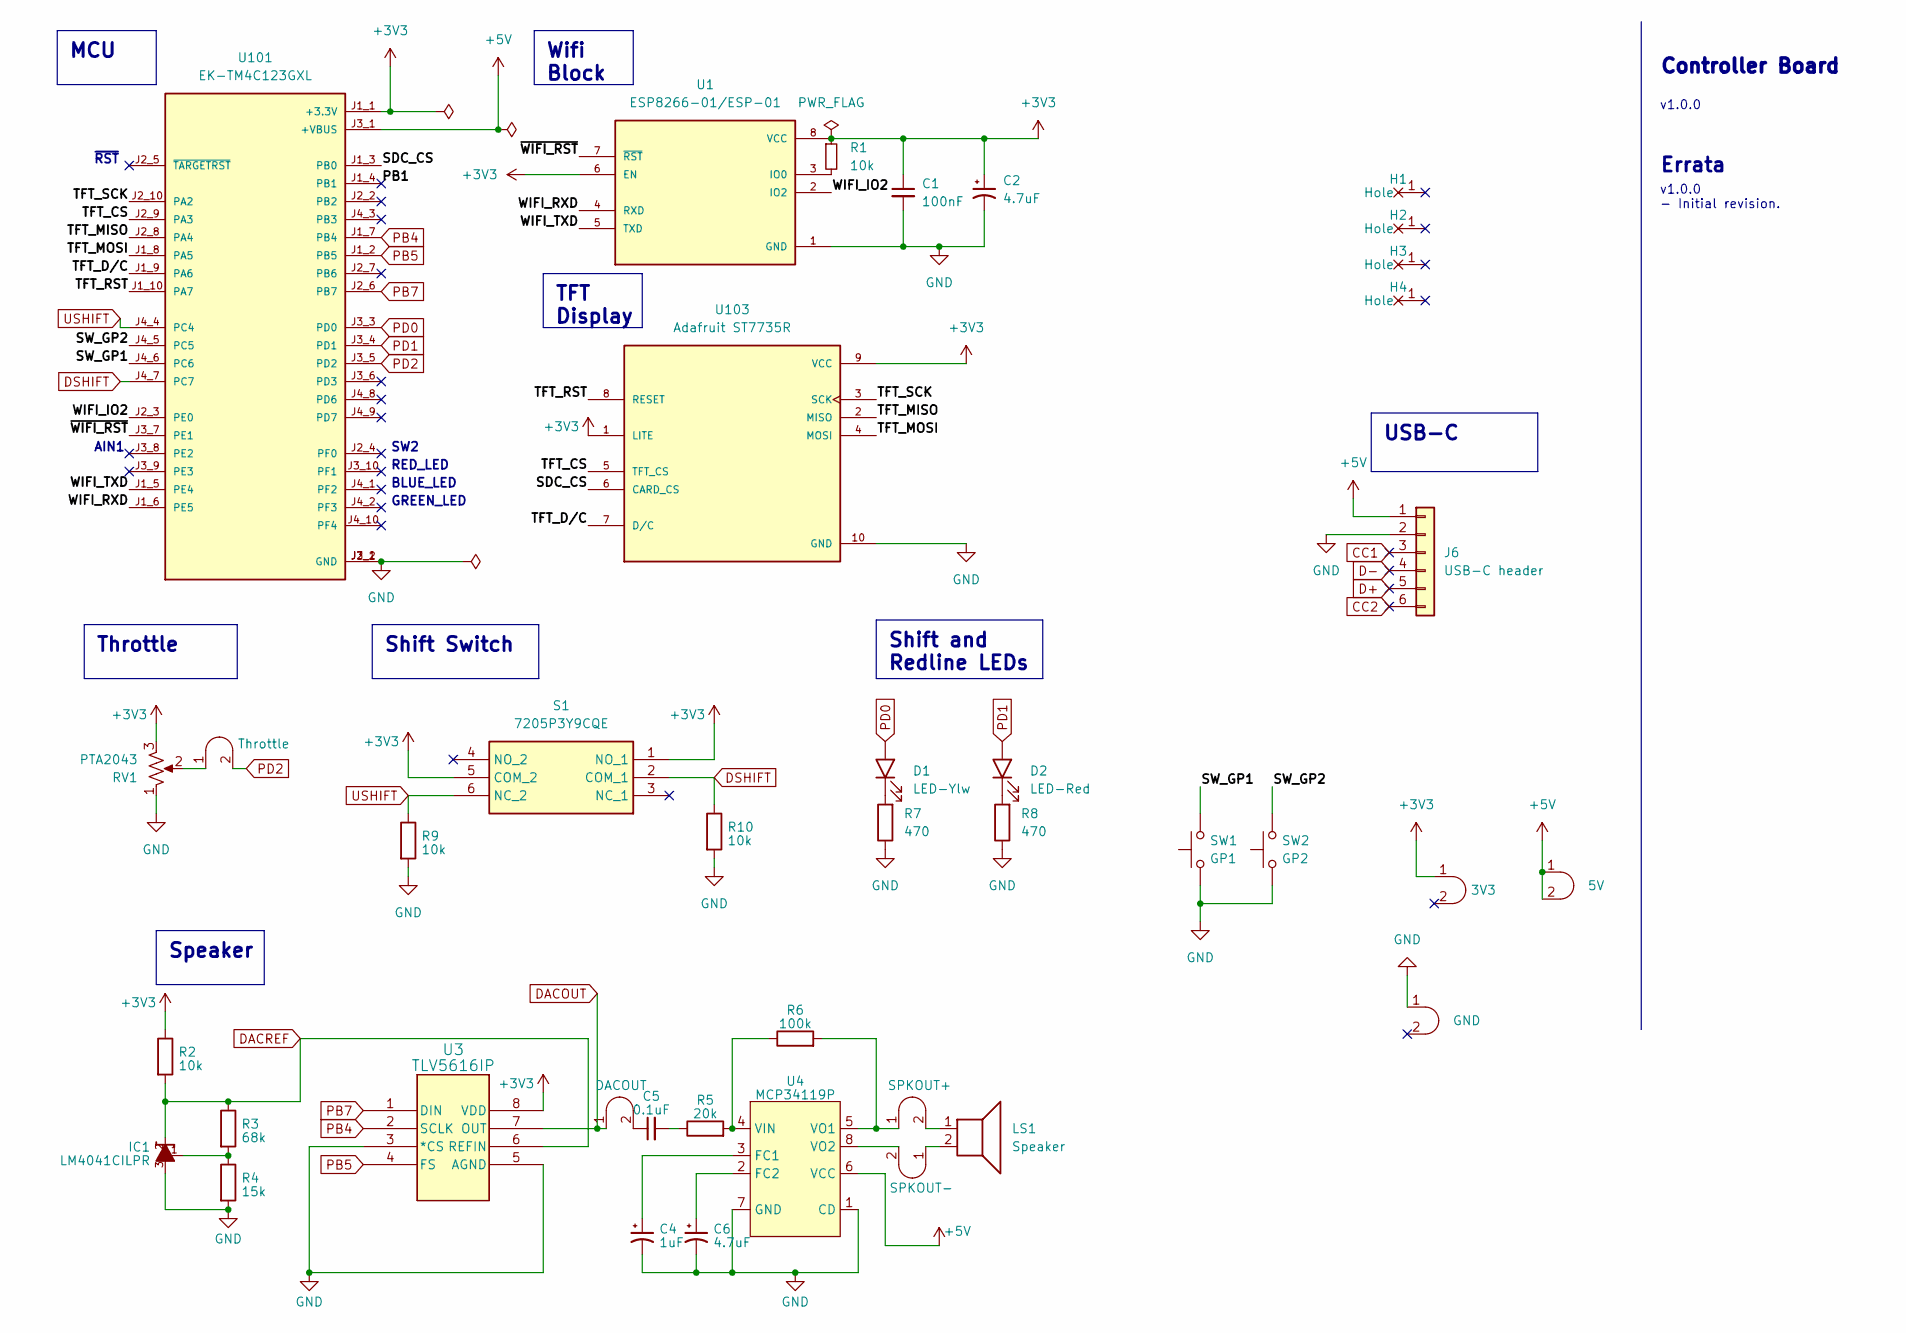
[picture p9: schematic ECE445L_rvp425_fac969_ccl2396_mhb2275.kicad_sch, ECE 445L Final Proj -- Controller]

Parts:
C1: 100nF; C_Axial_200mil
C2, C6: 4.7uF; C_Axial_200mil
C4: 1uF; C_Axial_200mil
C5: 0.1uF; C_Axial_200mil
D1: LED-Ylw; LED_D5.0mm
D2: LED-Red; LED_D5.0mm
H1, H2, H3, H4: MountingHole_4_40
IC1: LM4041CILPR; ti_LM4041CILPR
J1: Throttle; Testpoint_1x02_P2.54mm
J2: DACOUT; Testpoint_1x02_P2.54mm
J3: SPKOUT+; Testpoint_1x02_P2.54mm
J4: SPKOUT-; Testpoint_1x02_P2.54mm
J5: GND; Testpoint_1x02_P2.54mm
J6: USB-C header; PinHeader_1x06_P2.54mm_Vertical
J7: 3V3; Testpoint_1x02_P2.54mm
J8: 5V; Testpoint_1x02_P2.54mm
LS1: Speaker; PinHeader_1x02_P2.54mm_Vertical
R1, R2, R9, R10: 10k; R_Axial_DIN0204_L3.6mm_D1.6mm_P7.62mm_Horizontal
R3: 68k; R_Axial_DIN0204_L3.6mm_D1.6mm_P7.62mm_Horizontal
R4: 15k; R_Axial_DIN0204_L3.6mm_D1.6mm_P7.62mm_Horizontal
R5: 20k; R_Axial_DIN0204_L3.6mm_D1.6mm_P7.62mm_Horizontal
R6: 100k; R_Axial_DIN0204_L3.6mm_D1.6mm_P7.62mm_Horizontal
R7, R8: 470; R_Axial_DIN0204_L3.6mm_D1.6mm_P7.62mm_Horizontal
RV1: PTA2043; PTA2043pot
S1: 7205P3Y9CQE; Manufacturer_Part_Number 7205P3Y9CQE; Mouser Part Number 611-7205P3Y9CQE
SW1: GP1; Testpoint_1x02_P2.54mm
SW2: GP2; Testpoint_1x02_P2.54mm
U1: ESP8266-01/ESP-01; ai_thinker_ESP8266_01
U3: TLV5616IP; ti_TLV5616
U4: MCP34119P; DIP-8_W7.62mm_LongPads
U101: EK-TM4C123GXL; ti_EKTM4C123GXL
U103: Adafruit ST7735R; adafruit_st7735r

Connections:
+3V3: C1.1, C2.1, J7.1 (A), R1.1, R2.1, RV1.3, S1.1 (NO_1), S1.5 (COM_2), U1.6 (EN), U1.8 (VCC), U3.8 (VDD), U101.J1_1 (+3.3V), U103.1 (LITE), U103.9 (VCC)
+5V: J6.1, J8.1 (A), J8.2 (B), U4.6 (VCC), U101.J3_1 (+VBUS)
/PB1: U101.J1_4 (PB1)
/SDC_CS: U101.J1_3 (PB0), U103.6 (CARD_CS)
/SW_GP1: SW1.2, U101.J4_6 (PC6)
/SW_GP2: SW2.2, U101.J4_5 (PC5)
/TFT_CS: U101.J2_9 (PA3), U103.5 (TFT_CS)
/TFT_D/C: U101.J1_9 (PA6), U103.7 (D/C)
/TFT_MISO: U101.J2_8 (PA4), U103.2 (MISO)
/TFT_MOSI: U101.J1_8 (PA5), U103.4 (MOSI)
/TFT_RST: U101.J1_10 (PA7), U103.8 (RESET)
/TFT_SCK: U101.J2_10 (PA2), U103.3 (SCK)
/WIFI_IO2: U1.2 (IO2), U101.J2_3 (PE0)
/WIFI_RXD: U1.4 (RXD), U101.J1_6 (PE5)
/WIFI_TXD: U1.5 (TXD), U101.J1_5 (PE4)
/~WIFI_RST: U1.7 (~RST), U101.J3_7 (PE1)
CC1: J6.3
CC2: J6.6
D+: J6.5
D-: J6.4
DACOUT: J2.1 (A), U3.7 (OUT)
DACREF: IC1.2, R2.2, R3.1, U3.6 (REFIN)
DSHIFT: R10.1, S1.2 (COM_1), U101.J4_7 (PC7)
GND: C1.2, C2.2, C4.2, C6.2, IC1.3, J5.1 (A), J6.2, R4.2, R7.1, R8.1, R9.2, R10.2, RV1.1, SW1.1, SW2.1, U1.1 (GND), U3.3 (*CS), U3.5 (AGND), U4.1 (CD), U4.7 (GND), U101.J2_1 (GND), U101.J3_2 (GND), U103.10 (GND)
unnamed: C5.2, R5.1
unnamed: D1.1 (K), R7.2
unnamed: D2.1 (K), R8.2
unnamed: IC1.1, R3.2, R4.1
unnamed: J1.1 (A), RV1.2
unnamed: C5.1, J2.2 (B)
unnamed: J3.1 (A), R6.2, U4.5 (VO1)
unnamed: J3.2 (B), LS1.1
unnamed: J4.1 (A), LS1.2
unnamed: J4.2 (B), U4.8 (VO2)
unnamed: R1.2, U1.3 (IO0)
unnamed: C4.1, U4.3 (FC1)
unnamed: C6.1, U4.2 (FC2)
unnamed: R5.2, R6.1, U4.4 (VIN)
PB4: U3.2 (SCLK), U101.J1_7 (PB4)
PB5: U3.4 (FS), U101.J1_2 (PB5)
PB7: U3.1 (DIN), U101.J2_6 (PB7)
PD0: D1.2 (A), U101.J3_3 (PD0)
PD1: D2.2 (A), U101.J3_4 (PD1)
PD2: J1.2 (B), U101.J3_5 (PD2)
USHIFT: R9.1, S1.6 (NC_2), U101.J4_4 (PC4)

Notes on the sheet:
MCU
Throttle
Wifi Block
Shift Switch
TFT Display
USB-C
Shift and Redline LEDs
Speaker
v1.0.0 - Initial revision.
~{RST}
AIN1
Controller Board
v1.0.0
Errata
BLUE_LED
RED_LED
SW2
GREEN_LED

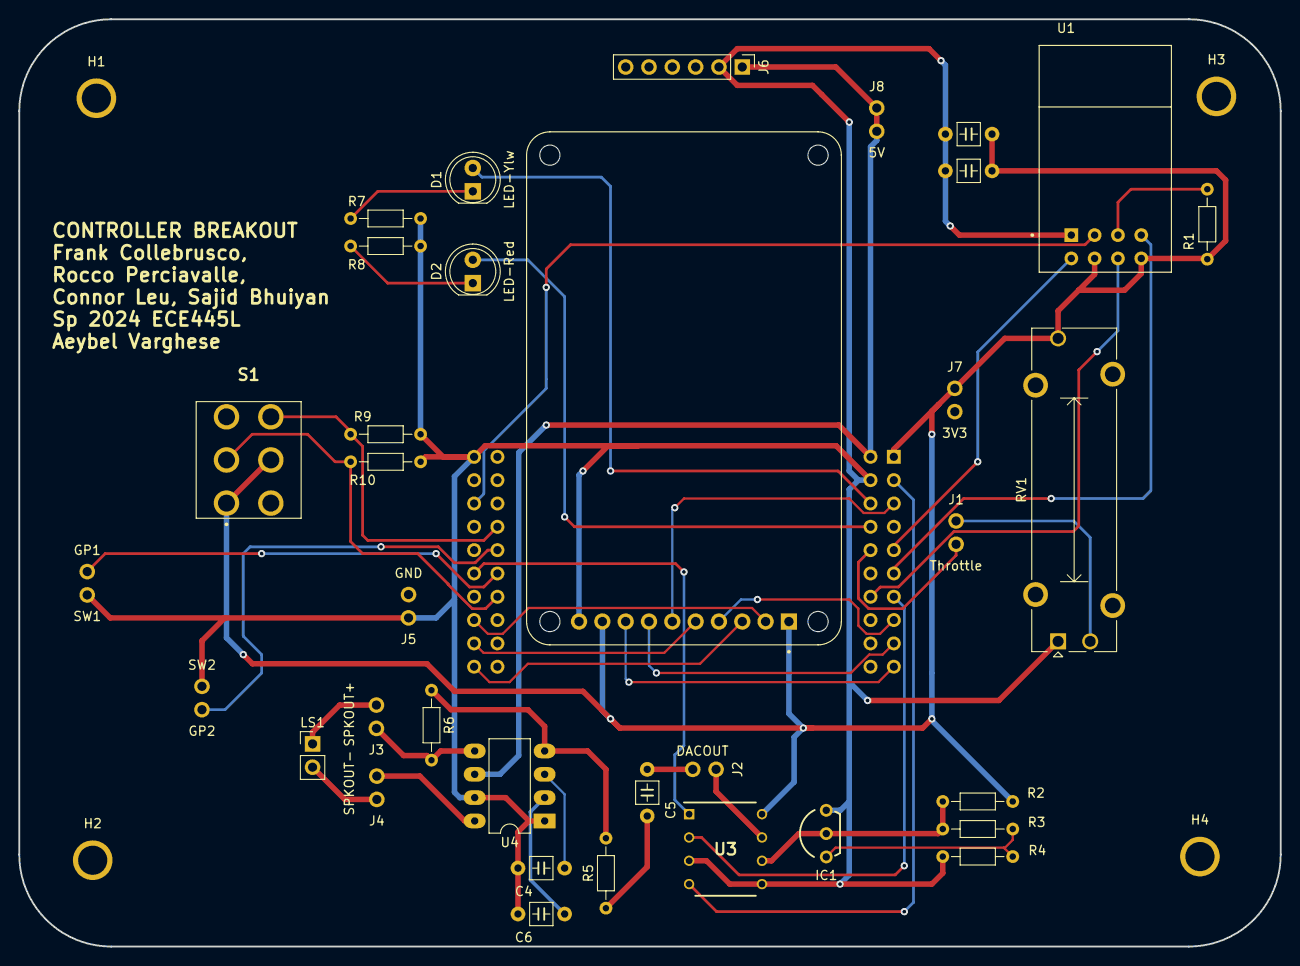
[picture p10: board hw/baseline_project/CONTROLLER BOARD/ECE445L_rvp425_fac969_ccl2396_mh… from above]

Board: 2 copper layers, 137.4 x 101.0 mm, 40 parts (1 on the bottom side), 40 nets.

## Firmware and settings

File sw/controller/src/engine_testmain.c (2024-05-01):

// /** File includes. */
// #include <stdint.h>

// /* Register definitions. */
// #include "../inc/tm4c123gh6pm.h"
// /* Clocking. */
// #include "../inc/PLL.h"
// /* Clock delay and interrupt control. */
// #include "../inc/CortexM.h"
// /* Initialization of all the pins. */
// #include "../inc/Unified_Port_Init.h"
// /* Talking to PC via UART. */
// #include "../inc/UART.h"
// /* ST7735 display. */
// #include "../inc/ST7735.h"

// #include "../inc/Timer5A.h"
// #include "../inc/Timer4A.h"
// #include "../inc/LED.h"
// #include "ControllerBoard.h"
// #include "Display.h"
// #include "DriveSim.h"
// #include "../inc/UART5.h"
// #include "../inc/esp8266_base.h"
// #include "EngineSound.h"


// /** Function Implementations. */
// static void DelayWait10ms(uint32_t n) {
//     uint32_t volatile time;
//     while (n){
//         time = 727240 * 2 / 91;  // 10msec
//         while (time){
//             --time;
//         }
//         --n;
//     }
// }

// #define PF1                     (*((volatile uint32_t *)0x40025008))
// #define PF2                     (*((volatile uint32_t *)0x40025010))
// #define PF3                     (*((volatile uint32_t *)0x40025020))

// static uint32_t flag = 0;
// static void frame_advance() {
//     if (flag) return;
//     flag = 1;
//     PF1 ^= 0x02;
//     controller_sample();
//     drive_throttle(controller_pot());
//     drive_step();
//     if (drive_rpm() >= 6000 && drive_rpm() <= 6500) 
//         controller_yellow_on();
//     else
//         controller_yellow_off();
//     if (drive_rpm() >= 6501) 
//         controller_red_on();
//     else
//         controller_red_off();
// }
// extern void drive_sim_dbgout();
// int testmain(void) {
//     DisableInterrupts();

//     PLL_Init(Bus80MHz);
//     UART_Init();
//     LED_Init();
//     draw_tach(700);
//     drive_init();
//     controller_init();
//     UART_Init();
//     UART5_Init();
//     Timer5A_Init(frame_advance, 80000000/30, 1);
//     Timer4A_Init(&tm4c_to_esp8266, 80000000, 4);
//     ST7735_InitR(INITR_REDTAB);
//     ST7735_FillScreen(ST7735_BLACK);
//     ST7735_SetCursor(0, 0);

//     EnableInterrupts();

//     EnableInterrupts();
//     uint32_t p_board = 0;
//     uint32_t sound = 1;
//     while (1) {
//         // PF3 ^= 0x08
//         if (flag) { flag = 0;
//             update_rpm(drive_rpm());
//             if (sound) engine_sound_up_rpm(drive_rpm());
//             uint32_t board = LaunchPad_Input();
//             if (p_board && !board) {
//                 sound = !sound;
//                 if (sound) engine_sound_start(drive_rpm());
//                 else engine_sound_stop();
//             }
//             p_board = board;
//             if (controller_lever_up()->falling)
//                 {drive_upshift(); update_gear(drive_gear());}
//             if (controller_lever_down()->falling)
//                 {drive_downshift(); update_gear(drive_gear());}
//                 drive_sim_dbgout();
//         }

//         WaitForInterrupt();
//     }
//     return 1;
// }

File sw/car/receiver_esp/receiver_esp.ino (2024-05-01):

#include <ESP8266WiFi.h>
#include <espnow.h>
#include <stdint.h>

#define RDY 2

// Callback function that will be executed when data is received
void OnDataRecv(uint8_t * mac, uint8_t *incomingData, uint8_t len) {
  Serial.write(*incomingData);
}
 
void setup() {
  Serial.begin(115200);
  
  WiFi.mode(WIFI_STA);

  pinMode(0, INPUT);
  pinMode(2, OUTPUT);
  digitalWrite(RDY, LOW);
  
  // Init ESP-NOW
  if (esp_now_init() != 0) {
    return;
  }
  
  esp_now_set_self_role(ESP_NOW_ROLE_SLAVE);
  esp_now_register_recv_cb(OnDataRecv);
  digitalWrite(RDY, HIGH);
}

void loop() {
  
}
